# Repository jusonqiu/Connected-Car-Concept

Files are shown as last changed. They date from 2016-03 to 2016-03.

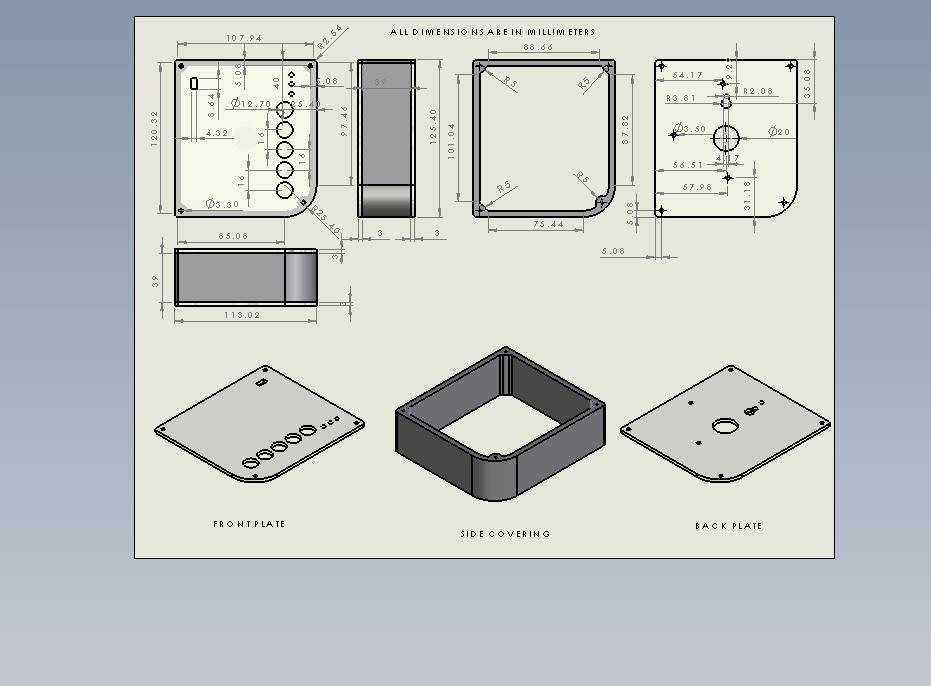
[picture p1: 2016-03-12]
Case Enclosure/Engineering Drawing.jpg

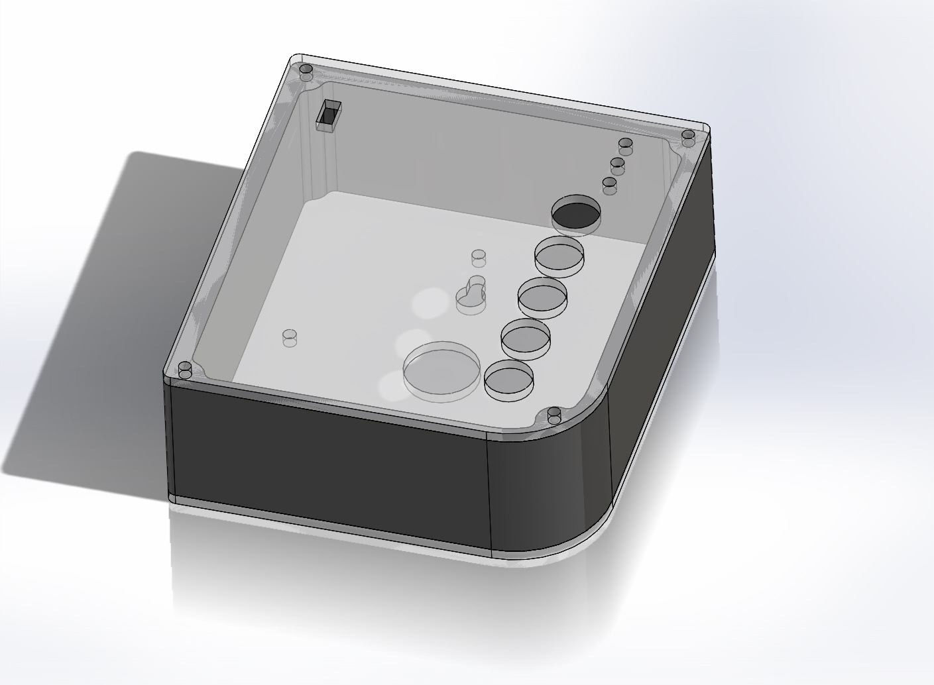
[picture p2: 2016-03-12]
Case Enclosure/GateBox Model.JPG

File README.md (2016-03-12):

# Connected Car Concept

The Connected Car Project, GateBox, allows you to operate your garage door and front lawn lights from the car's dashboard itself. It does this by having a smartphone interact with a gateway panel (the GateBox panel) that is placed within the garage. The smartphone is mirrored onto the car's dashboard. This is possible using a number of Connected Car features which are likely to grow popular in the future such as: Android Auto, Apple CarPlay, MirrorLink, AppLink, etc. This project was entered into the Microsoft Imagine Cup competition of 2015.

Please watch the introduction video below:

<div style="text-align: center">
<a href="http://www.youtube.com/watch?feature=player_embedded&v=YNrUQAdRSC8
" target="_blank">Connected Car Demonstration</a>
</div>

The Github.io page is can be seen [here](http://shafeeqr2.github.io/Connected-Car-Concept/ "GateBox").
## Opensource
Since the Microsoft Imagine Cup competition, this project has been released on Github in hopes that it can be improved upon. The orignal app developed is in the "Windows Application Folder". Some of the files that were submitted to Microsoft judges are in the "Imagine Cup Files" folder. These files have been slightly modified since submission. 

## Where to Start?
First read the Bluetooth manuals. They are from the Bluetooth Special Interest Group and aim to teach how to develop Bluetooth Low Energy applications for a number of different platforms  - Android, iOS and Windows Phone.

For the electronics, there are two different ways to approach this project: The Simplified and Detailed way - One method uses a pre-existing Bluetooth LE chip and other method involves making this chip from scratch based on schematics provided. There is a Parts List and the Instructions version for the detailed and the simplified way. It is recommended that you start with the simplified way even if you plan to use the detailed way.

Read through the parts list for the electronics and the case enclosure in the "Parts List" folder. Then, read through the hardware and software instructions in the "Instructions" folder.

##Contribute

If you feel you can improve on a certain aspect of this project or expand upon it, please considering sharing it to be a part of this project.

If you have any questions or concerns, please contact me at: shafeeqr21@gmail.com.

## What are Connected Cars?

### The following expert is from a 2014 CABA (Continental Automated Building Association) report:

*The connected car market, while still in its infancy, has rapidly evolved from a niche capability available in select models to a perceived must-have in the car industry. A connected car, by definition, is one that maintains a wide area connection (typically cellular-based) and often also a local area network (typically Wi-Fi). Via these connections the car is able to send and receive information relevant to the trip/route and the car’s performance/condition.*

*An increasing number of vehicles are coming to market with the capability to support communications of various sorts. In 2013 more than one billion sensors were sold to the auto industry, more than doubling the 2009 levels[1]. While tethered and integrated solutions have dominated car connectivity to date, embedded connectivity solutions began appearing in 2014 with the number of such vehicles increasing in 2015 and beyond.*

*The connected car market is on the cusp of significant growth. A variety of market factors, from government regulations, to industry partnerships, to consumer demand, are propelling the connected car market forward. Consumers got a glimpse of the future of connected cars in 2014 as select models began rolling off the production line with these capabilities, but 2015 promises so much more in terms of number of connected vehicles and the services being delivered to those vehicles.* 

##

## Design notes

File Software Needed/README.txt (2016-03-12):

The Arduino v 1.0.6 and nRFgo Studio are available for download at the following link: https://goo.gl/C3nlrD

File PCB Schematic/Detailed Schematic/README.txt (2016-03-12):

The design has been modified since these files have been made.

Would appreciate it if someone could replace the two solid state relays with 4 mechanical relays (as shown in PCB V7 board.PNG in Simplified Schematic folder) and re-route all the wires and push the .brd and .sch files.

Thanks.

Shafeeq.

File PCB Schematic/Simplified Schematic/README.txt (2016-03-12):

The design can be further simplified if you decide to use your own Arduino UNO in which case you need not include the following materials onto PCB (Refer to "PCB V7 board.PNG"):

* DCJACK
* Diode D1
* Capacitors C1, C2, C3, C4
* ATMEGA328P IC1
* Voltage Regulator 7805T IC2
* Quartz Crystal 16MHZ Q1

It would be nice if someone can take the time to make a PCB without these items and in its place leave a line of male headers which would connect to the Arduino UNO as per the following pinouts:

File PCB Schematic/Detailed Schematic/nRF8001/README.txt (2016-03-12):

The schematics of Adafruit's nRF8001 Bluetooth Low Energy Module circuitry can be found on 

Adafruit's Github Repository: https://github.com/adafruit/Adafruit-Bluefruit-LE-nRF8001-PCB

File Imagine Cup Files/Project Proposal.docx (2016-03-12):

GATEBOX

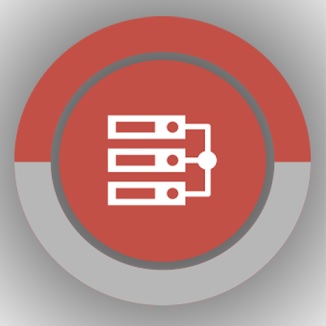
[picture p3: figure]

Shafeeq Rabbani

Paul Calinescu

Edgar Malchic

Esther Baruti

Why are we doing this?

We would like to make a positive impact in millions of households in the coming years by making the lives of homeowners more convenient and providing them with more control over their homes.

How are we going to do this?

Today, we have smartphones that can operate Bluetooth peripherals in a house and cars which can be paired with smartphones. Such cars are commonly referred to as connected cars. We would like to combine these two so that your connected car interacts with your house.

What are we making?

The GateBox.

There are two components to this system. First, is the panel which sits into the garage of your home. The second is the Windows Phone app which interacts with the panel in order to do some pretty interesting things in the garage.

Now, I know what you are thinking. How does the car enter the picture?

Currently, in the connected car market, solutions such as MirrorLink by Car Connectivity Consortium, AppLink by Ford, Android Auto by Google and CarPlay by Apple are gaining momentum. These solutions are meant to project the screen of the smartphone onto the dashboard of the car.

Before we go into details, we would like to demonstrate this system to you.

When the driver approaches the house, the app automatically detects the peripheral and connects to it. The driver, who is now in the driveway, is prompted to enter a passkey. Upon correct entry, the driver gains access to the control panel. From here, the driver can operate the garage door and the lights.

The Panel acts as a Bluetooth Low Energy peripheral and the smartphone acts as the central. We are using a custom GATT service.

The field of home automation along with connected cars is about to boom. According to the Continental Automated Buildings Association or CABA, the timing of this boom is put somewhere between late 2014 and mid 2015.

Hence, this is the best time for a system such as the GateBox. Our product touches on both matters, contributing and expanding this imminent boom.

The market for this system is geared towards people who live in homes with attached garages and drive cars.

Connected cars is a technology that will increase the intelligence of existing home automation systems. A more connected system will have a significant potential of becoming a smarter system. For a long time, your garage and your car have been two different systems. Now is the time to link these two systems so that you can control your garage door and garage lights directly from the car dash.

There has been talk in the market of connecting smartphones with cars with solutions such as MirrorLink from the Car Connectivity Consortium, and AppLink from Ford. We would like to take it one step further and connect your car with your garage.

Although there are a handful of similar projects we have encountered, none of them show signs of being consumer ready like the GateBox.

A system like this serves as a base that can easily be expanded upon in the future. In the future, we intend to further expand the capabilities of this product. It will have an IP address allowing it to connect to the network. That would allow us to collect data of this device to better serve the consumer. We would also like to give this product BACnet interoperability. BACnet is a communication protocol used in Building automation.

There are cars in the market today which have their own internet connection (I’m not sure about WIFI). Chevrolet is one of the manufacturers which are pushing for this. This option is available in models starting around the $15,000. Possible uses include having anonymous, critical and/or sensitive data uploaded to the cloud. This app which resides on your data-enabled smartphone and therefore our system would allow us to communicate with our car even when we are not home (i.e. work).

Our system is meant to be easily implemented in most garage with basic knowledge. The configuration of the system is meant to be intuitive and user friendly.

In addition to having full control of your garage and lights via your car, the GateBox panel located inside the garage will have physical switches mounted onto it allowing the homeowner manual control of their garage and lights.

GETTING PRODUCT INTO MARKET

Making an App for a car platform is a little bit more complex than making one for a smartphone. Not every smartphone platform is compatible with every mirroring software. Hence, in order to gain a broad consumer base, our app must be available in a number of smartphone platforms.

So how does Microsoft fit into this? Last year, Microsoft demonstrated the compatibility of Windows Phone with a MirrorLink-like solution. Considering their long partnership and contribution with the Car Connectivity Consortium the Windows Phone solution to MirrorLink may just be around the corner.

And while the Mirroring software industry is likely to grow exponentially in the coming years, we cannot ignore the already existing massive consumer base with Windows Automotive and QNX Car Infotainment systems present today which numbers in the tens of millions. We know exactly how to go about developing and testing our software application for inbuilt car infotainment systems and the costs involved. We are currently looking for auto manufacturers who are interested in implementing the GateBox software application.

We have a carried out a detailed research of every registration, certification and testing procedure we have to carry out in order to bring this product to the shelves. We are well aware of the procedures involved such as listing by Bluetooth Special Interest Group, electrical certification by the CSA group, Qualification by MirrorLink and AppLink, testing center fees and others related to registering a corporation. The details of these procedures and their cost are mentioned in our document. If we win the prize money, we have a very good idea of how we intend how to spend it in order to bring GateBox to the market.

The time is right for your car to join the smart movement. We see car manufacturers such as Chevrolet provide 4G LTE connectivity in cars starting from around $15,000. This will effectively put cars on the web and therefore make them accessible from anywhere. We see a future where we can control many of the things that we have never thought of controlling. Imagine being able to control things such as your sprinkler system if you don’t want it to turn on because it already rained that day. How about controlling your blinds because your house is letting you know that the sun is too bright and it would contribute to hotter temperatures inside the house. And what if you’ve forgotten your lights on in the house while you left in a hurry? Our system, the GateBox, will eventually be able to relay that information to your data enabled smartphone. What started as a system which can control your garage and lights could potentially turn into something which can solve many of our past, present and future problems and simplify our everyday tasks.

HOW WILL WE SPEND THE PRIZE MONEY IF WE WIN?

Task | Description | Cost
Registration as Corporation | Registration the corporation at Canadian Federal level with name search. | $250 CAD
Bluetooth Compliance Fees | Requirement to use Bluetooth product and will give us permission to use logo. For adopter members, the fee is $8000. However, as we would be a new company, we qualify for their Innovation Incentive Program (IIP) bringing the fees down to $2500. | $2500 USD
Bluetooth Testing and Bluetooth Qualification Review | This is carried out by a certified testing center of Bluetooth. We have been in contact with a testing center interested in testing our device. They have given us a quote of $6550. | $6650 USD
MirrorLink testing and certification | Testing is carried out by a certified body. Certification of our apps will allow the Android to work with ever growing MirrorLink installed car dashboards. | $ 5839.26 USD (or less if it is determined that app is not as complex).
Representative Business travel across US and Canada over a period of 2 years. | These are to establish business links with car manufacturers and other companies alike who are interested in partnering with us on mass production of the GateBox over a period | $10,000 USD
Purchase Pioneer Appradio 4 | This would be done to use for testing of our AppLink. | $600 USD
Testing for AppLink | Testing for Ford AppLink is carried out by a certified testing centre. AppLink is compatible with 3 smartphone platforms.i.e. Android, iOS and Blackberry. | $1400 x 3 = $4200 USD
Profile Tuning Suite Radio Module | This device is used for Bluetooth by ourselves before we send it out to the testing centre. It must be purchased from http://bluetoothstore.org/. | $99 USD
Safety certification of electrical product | We have sent the appropriate documentation for testing so that they can provide us with a quote. | $2500 USD
Software developer registration | Apple developer registration, Windows developer registration, Android developer registration and Blackberry developer registration for 3 consecutive years.
Purchasing software with commercial licenses
Purchasing smartphones for testing on different platforms | Alongside Windows Phone, we would like to test in Blackberry, Android and iOS. | $2000 USD
The remaining amount will be spent on costs we did not previously anticipate.

ELECTRONICS BEHIND THE GATEBOX

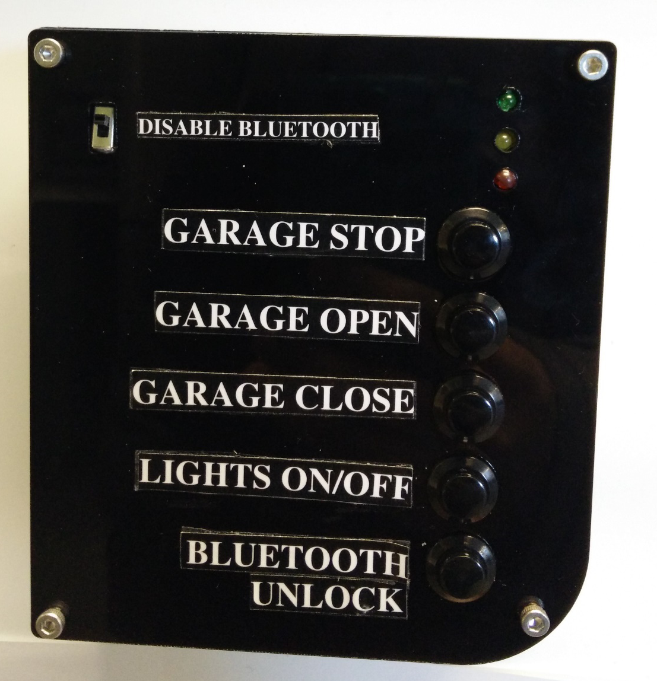
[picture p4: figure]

The GateBox panel is used to control the homeowner's garage door. Within the panel there is a custom relay shield that is controlled by a micro controller. On the main panel, there are 5 buttons. The 3 of the 5 buttons are used to stop, open, or close your garage. The fourth button is used to control the lights and the fifth button is used to unlock your Bluetooth panel. The sliding switch located at the top left is placed there for security purposes. If the homeowner decides to go on vacation and wants their panel to stop broadcasting, all they have to do is toggle the switch down. The LEDs are indicators to show an established connection between the panel and the car. The electronics inside the panel are:

1. main board
  a. This board consists of 4 mechanical relays, 5 push buttons, a barrel jack for power, a voltage regulator, resistors, diodes, capacitors, transistors etc. Please see parts list. The main board is powered by a 9V dc barrel jack adapter.
2. LED board which is attached to the main board by jumper cables.
3. Bluetooth low energy chip (nRF 8001 from Nordic) which is connected to the main board through header pins.

The device is meant to be up and running 24/7. Of the four mechanical relays, three are normally open and one is normally closed.

Button | State | Voltage
Garage Door Stop Button | Normally Closed | 0 - 24 VDC
Garage Door Open Button | Normally Open | 0 - 24 VDC
Garage Door Close Button | Normally Open | 0 - 24 VDC
Lights Button | Normally Open | 120 - 240 VAC

These relays can be operated by the push buttons or a command from the homeowner’s smartphone which is received by Bluetooth Low Energy chip. In either case, the command is first sent to the ATMega328PU microcontroller first which then sends a signal to the relay.

The enclosure of this device is made of 3mm thick acrylic. The device is meant to be wall mounted at least 5 feet above the ground.

The panel is compatible with most garage openers on the market today such as Liftmaster or Chamberlain. The contacts of the garage door and lights can be directly wired into the terminal blocks of the relay shield, and then the homeowner can begin accessing their garage door and lights via their car. We see a brilliant future where the world around us is further connected with smart sensors and devices which allow for a smoother and more effective interaction with the world around us.

Custom Board Bill of Materials

| | | | Total Costs | $28.7778
Part | Digikey/ Element14 Part No. | Manufacturer Part No. | Quantity | Picture | Cost
Atmega 328p Microcontroller | 68T2944 | ATMEGA328P-PU | 1 | | $3.24
16 MHz Crystal Oscillator | 18C1481 | XT9S20ANA16M | 1 | | $0.338
28 pin DIP IC Socket | 34P8056 | 4828-3004-CP | 1 | | $0.503
Rectifier Diode 1A, 50V | 10M8464 | 1N4001 | 1 | | $0.113
LM-7805-CT Voltage Reg. | MC7805CTG | MC7805CT-BPMS-ND | 1 | | $0.487
Switch Tactile SPST-NO | MJTP1230 | 679-2428-ND | 2 | | $0.1124
Terminal blocks | ED1623-ND | ED500/2DS | 4 | | $0.85
2.1mm DC Barrel Jack | CP-037A-ND | PJ-037A | 1 | | $1.23
100uF, 25V Electrolytic Cap. | 39T8695 | 25YXH100MEFC6.3X11 | 2 | | $0.075
22 pF, 50 V Ceramic Cap. | BC1034TR-ND | K220J15C0GF5TH5 | 2 | | $0.34
3mm LED, FWD V= 2.1V/I= 20 mA | 94T8843 | 703-0087 | 3 | | $0.184
10K Ω Resistor, 1W, 5% | 95W5667 | CFR100J10K | 8 | | $0.18
1K Ω Resistor, 1/4W, 5% | 25M8365 | CBT25J1K0 | 7 | | $0.32
6 Pin Male Header | 609-3263-ND | 68000-406HLF | 4 | | $0.24
G5V-1-DC Low Signal Relay | Z773-ND | G5V-1-DC5 | 4 | | $2.77
SPDT Sliding Switch | CKN9565-ND | OS102011MS2QN1 | 1 | | $0.54
DIODE GEN PURP | 1N4148TACT-ND | 1N4148TA | 4 | | $0.14
Transistor NPN | 2N3904FS-ND | 2N3904BU | 4 | | $0.26

NRF8001 BLE Board Bill of Materials

| | | | Total Costs | $23.7681
Part | Digikey/ Element 14/ Mouser Part No. | Manufacturer Part No. | Quantity | Picture | Cost
BLUETOOTH LW ENERGY nRF 8001 | 1490-1026-ND | nRF8001-R2Q32-T | 1 | | $5.72
HIGH-LOW LEVEL SHIFTER | 568-8150-1-ND | 74HC4050D,653 | 1 | | $0.606
Capacitors Solid SMD 10uF | 718-1126-2-ND | 293D106X96R3A2TE3 | 2 | | $0.229
LDO Voltage Regulators High | 576-2980-2-ND | MIC5225-3.3YM5 TR | 1 | | $1.28
CAPACITOR 15PF 50V, C0G, 5%, 0402 | 38K1652 | GRM1555C1H150JZ01D | 4 | | $0.106
CRYSTAL 32.7KHZ 12.5PF SMD | SE2415CT-ND | FC-255 32.7680K-A3 | 1 | | $1.69
Capacitor SMD 33 nF 25 VDC 0402 | 65-754-51 | GRM155R71E333KA88D | 1 | | $ 0.683
CAPACITOR, 0402 0.1NF 50V | 578095 | CM05CG101J50AH | 2 | | $1.00
Capacitor SMD 0.1uF 25volts | 478-7868-1-ND | 04023C104KAT2A | 1 | | $0.471
CAP, MLCC, X7R, 1NF, 50V, 0402 | 490-1303-1-ND | GRM155R71H102KA01D | 1 | | $0.368
CAP SMD 10UF 6.3V 20% 0402 | 81-GRM155R60J106ME4D | GRM155R60J106ME44D | 1 | | $0.444
CAP, 1.5pF 50V C0G ±0.1pF SMD | 490-8087-1-ND | GJM1555C1H1R5BB01D | 1 | | $0.10
CAP SMD 0402 22pF 50V C0G 5% | 581-04025A220J | 04025A220JAT2A | 1 | | $0.135
CAP SMD 0402 1.8pF 50V C0G | 81-GJM1555C1H1R8BB01 | GJM1555C1H1R8BB01D | 1 | | $0.283
CAP, MLCC, 2.2NF, 50V, X7R, 0402 | 2310511 | MC0402B222J500CT | 1 | | $0.11
RESISTOR, 10K, 0.06W, 0402, SMD | 541-10.0KLCT-ND | CRCW040210K0FKED | 1 | | $0.59
RES SMD 22K OHM 0.1% 1/10W 0603 | P22KDBCT-ND | ERA-3AEB223V | 1 | | $0.91
EMI Filter Beads, Chips & Arrays | 810-MMZ1608B121C | MMZ1608B121C | 1 | | $0.135
8.2nH SMD Inductor, 4.9GHz | 810-MHQ1005P8N2JT | MHQ1005P8N2JT | 1 | | $0.34
INDUCTOR, 10NH, 2%, 3.9GHZ, SMD | 994-0402CS-10NXGLU | 0402CS-10NXGLU | 1 | | $1.69
INDUCTOR, 15NH, 5%, 3.28GHZ, SMD | 994-0402CS-15NXJLU | 0402CS-15NXJLU | 1 | | $1.40
INDUCTOR,3.9NH, 5%, 9.5GHZ, SMD | 994-0402HP-3N9XJLU | 0402HP-3N9XJLU | 1 | | $1.54
INDUCTOR, 5.6NH, 2%, 6.5GHZ, SMD | 994-0402HP-5N6XGLU | 0402HP-5N6XGLU | 1 | | $1.34
CRYSTAL 16MHZ 9PF SMD | SER3636CT-ND | TSX-3225 16.0000MF18X-AC | 1 | | $0.91
U.FL SMD Antenna Connector | 798-U.FL-R-SMT10 | U.FL-R-SMT(10) | 1 | | $1.59

Schematic of Custom Board (created using Eagle CAD)

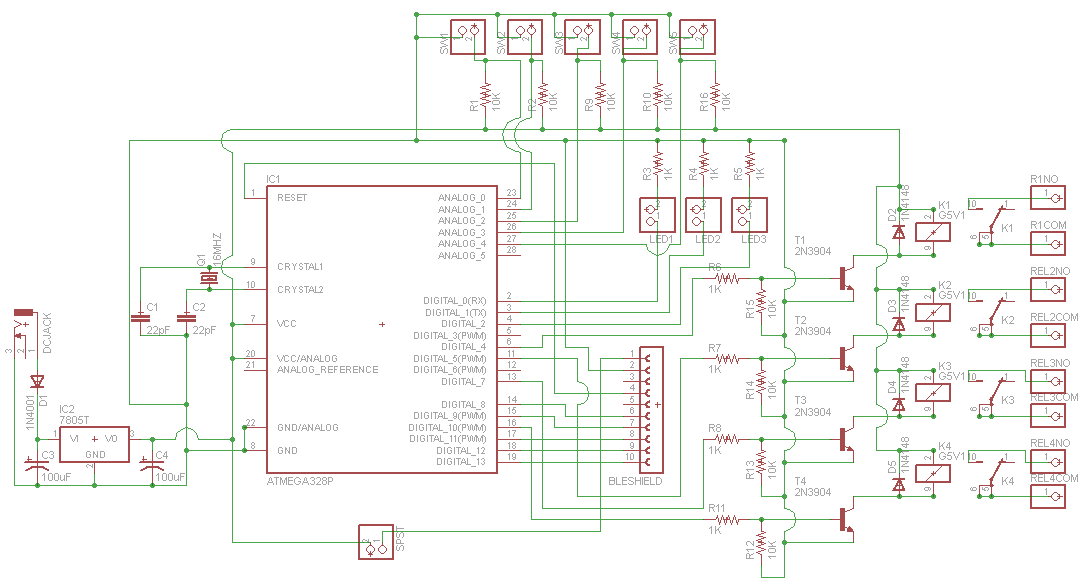
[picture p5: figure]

Layout of PCB (created using Eagle CAD)

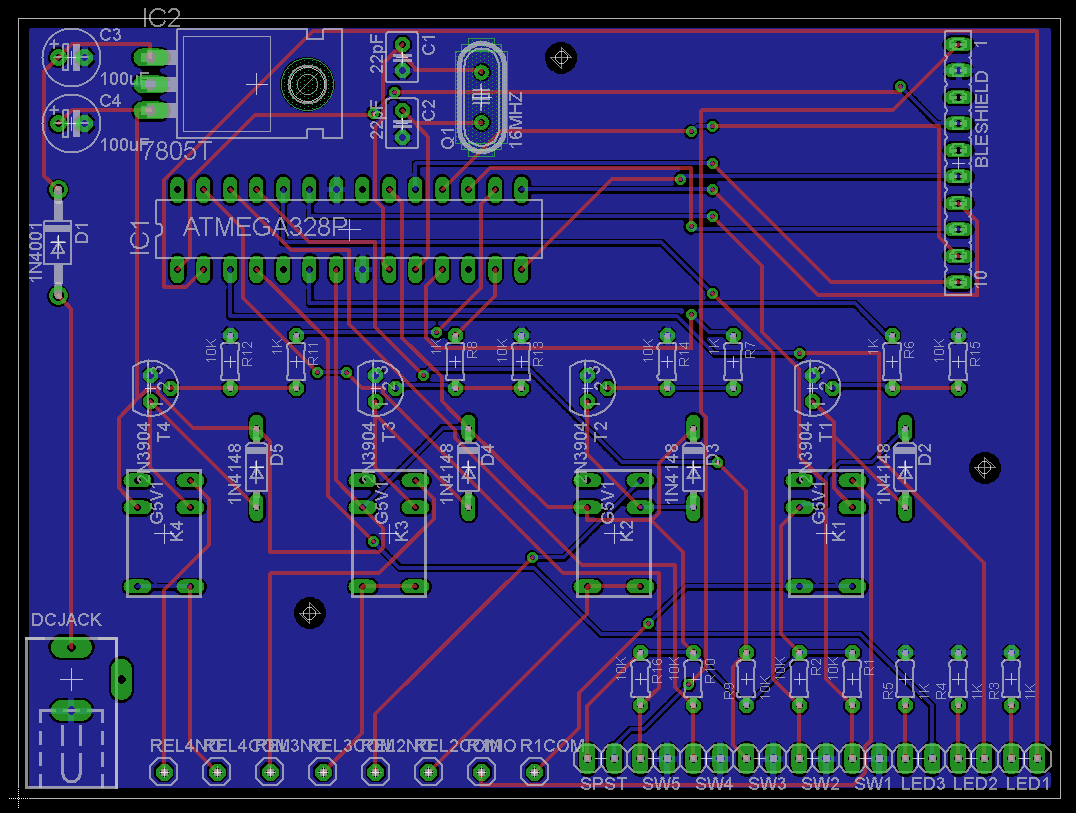
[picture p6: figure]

The GateBox panel was designed in Solidworks

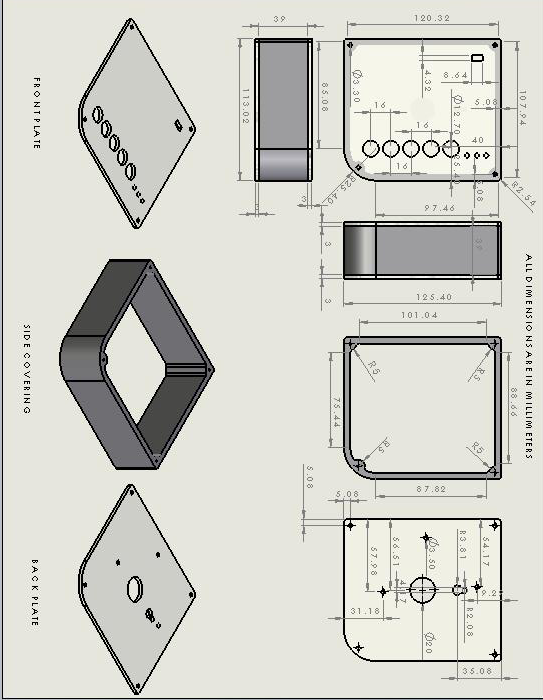
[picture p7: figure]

Safety Concerns

- The wall console/push button should be mounted at least five feet from the floor and the remote controls should be kept out of the hands of children. Children should never be allowed to play with or use the garage door opener remotes or wall pushbuttons. Homeowners should also keep a moving door in sight until it fully opens or closes.

Source: http://www.dasma.com/safetygdguide.asp

- Must be installed by a licensed electrician.
- Do not run any low voltage control wires close to the 120-volt power line. Do not run any wires through the same holes as the 120-volt power line in studs or cross ties. Either of these conditions will not comply with the NEC and may interfere with safe operation of the garage door operator.
- You will need 3 lengths of 2 conductor color coded minimum 22-gauge bell wire (phone wire) suitable for Class 2 installation. In Canada, this wire must be CSA certified.
- Emergency Stop button allows for the door to stop immediately whether it is going up or down.

Emergency Stop Button

Other Similar Projects/Products

HomeLink | http://homelink.com/home/welcome
Bosch Hackathon 2nd Place Winner (Not a competitor, has not produced a product out of this demo). | http://blog.bosch-si.com/categories/mobility/2014/10/how-can-we-bring-the-garage-into-the-car/
Other systems allow door activation over the Internet to allow home owners to open their garage door from their office for deliveries. | https://www.liftmaster.com/For-Homes/Garage-Door-Openers/Elite-Series/model-8550
The Overhead Door® Advanced Wall Console has been designed to not only provide homeowners with advanced security, but to deliver more control over their garage door opener, its lighting and opener performance status. The console is programmable to provide service reminders and contact information for the local Overhead Door Red Ribbon Distributor, making annual maintenance easy and convenient. | http://www.overheaddoor.com/garage-door-openers/Pages/advanced-wall-console.aspx http://www.overheaddoor.com/garage-door-openers/Pages/garage-door-opener-accessories.aspx
Bluetooth switch | http://www.ablenetinc.com/Assistive-Technology/Computer-Access/Blue2-Bluetooth-Switch
My door open iPhone app | https://itunes.apple.com/en/app/mydooropener-elite/id359774310?mt=8
iWUP | http://www.instructables.com/id/Garage-Door-Opener-with-iphone-Arduino-project/?ALLSTEPS

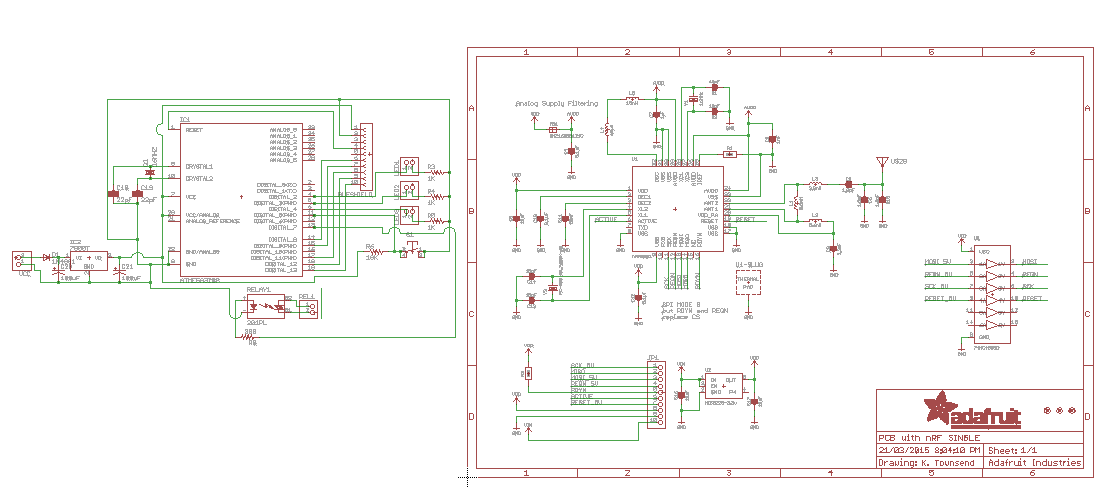
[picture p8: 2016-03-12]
PCB Schematic/Detailed Schematic/PCB with nRF/SINGLE RELAY/PCB with nRF Single Schematic.PNG

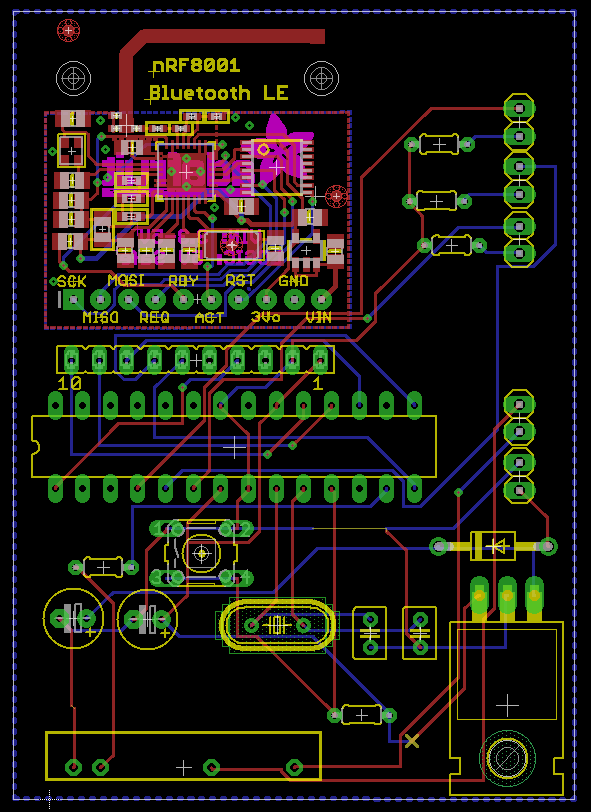
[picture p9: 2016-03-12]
PCB Schematic/Detailed Schematic/PCB with nRF/SINGLE RELAY/PCB with nRF Single Board.PNG

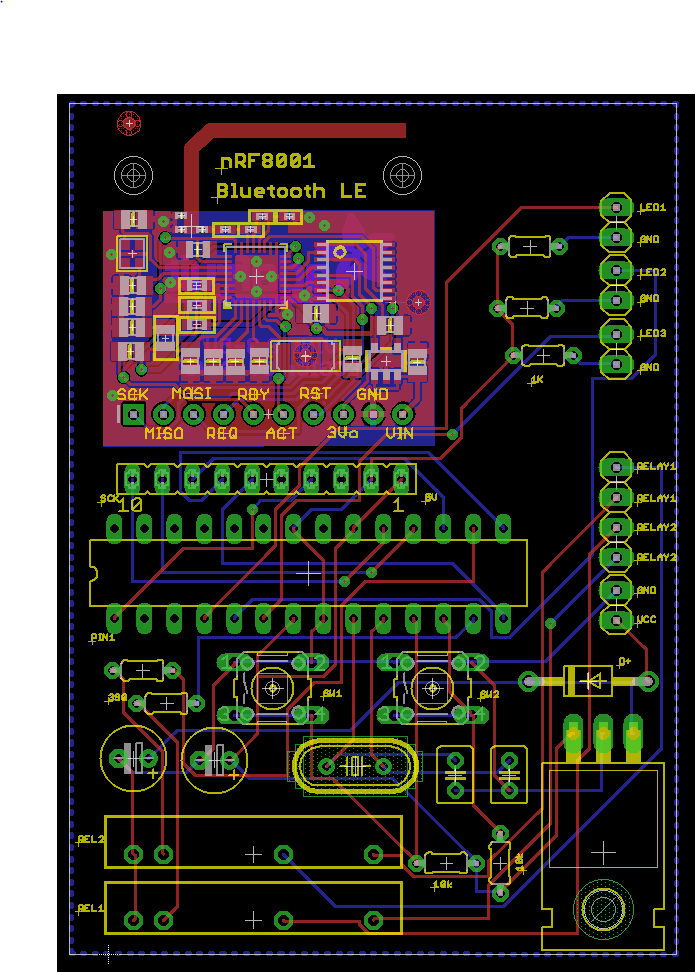
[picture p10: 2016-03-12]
PCB Schematic/Detailed Schematic/PCB with nRF/DUAL RELAY/PCB wih nRF board labeled.PNG

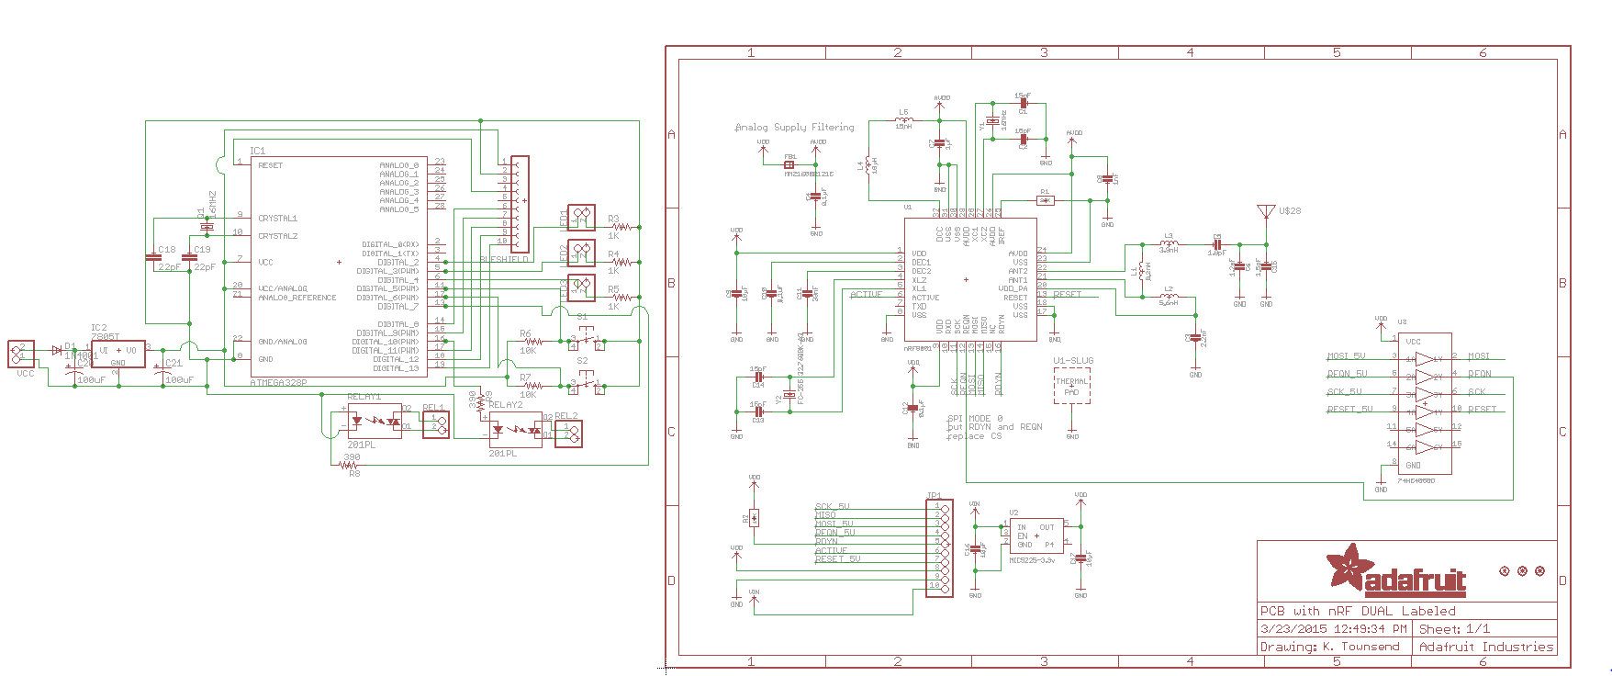
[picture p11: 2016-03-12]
PCB Schematic/Detailed Schematic/PCB with nRF/DUAL RELAY/PCB wih nRF schematic labeled.PNG

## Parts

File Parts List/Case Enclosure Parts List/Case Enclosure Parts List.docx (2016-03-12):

CASE ENCLOSURE PARTS LIST

You will need:

1. Access to a CNC machine
2. Access to 3D printer w/ ABS filament (preferably black colored filament)
3. M3-0.5 x 10mm DIN 912 Hex Drive Grade A2-70 Stainless Steel Socket Cap Screw (8 pieces)

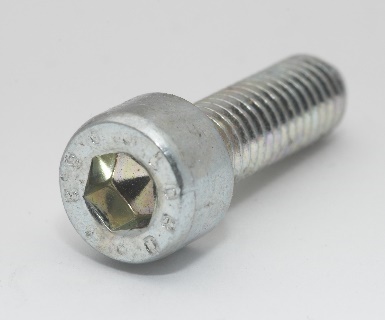
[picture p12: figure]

4. 3mm thick square acrylic plates (15 cm x 15 cm) (2 pieces) preferably black colored and glossy.
5. 3mm tap drill bit and a tapping drill

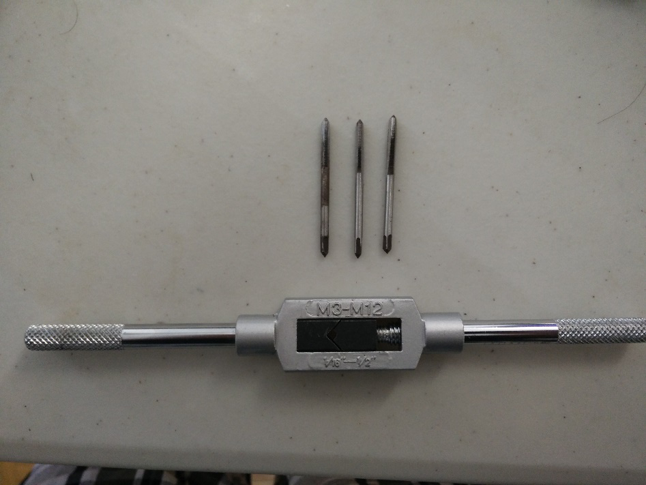
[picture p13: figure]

6. Allen key
7. Glue gun

CASE enclosure consists of the following parts:

A. The front plate
B. The back plate
C. The Covering

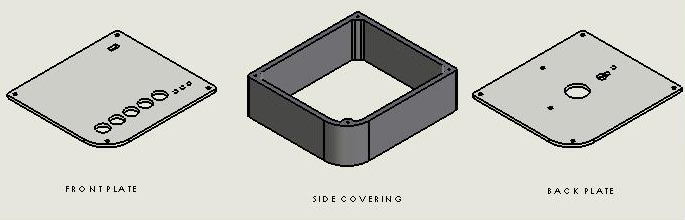
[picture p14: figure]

Instructions:

1. The front plate and back plate are 3mm thick acrylic plates (preferably black colored). Use the STEP files in the Case Enclosure Folder. The front_plate.STEP file back_plate.STEP file have to used to cut the acrylic plates into shape using a CNC.
2. The side_covering.STL file must be 3D printed with ABS filament.
3. Using the 3mm tapping drill bits and the hand tapping tool, carefully thread the 8 holes (4 on each side) of the side_covering.
4. Place the front panel on the side covering as shown below:

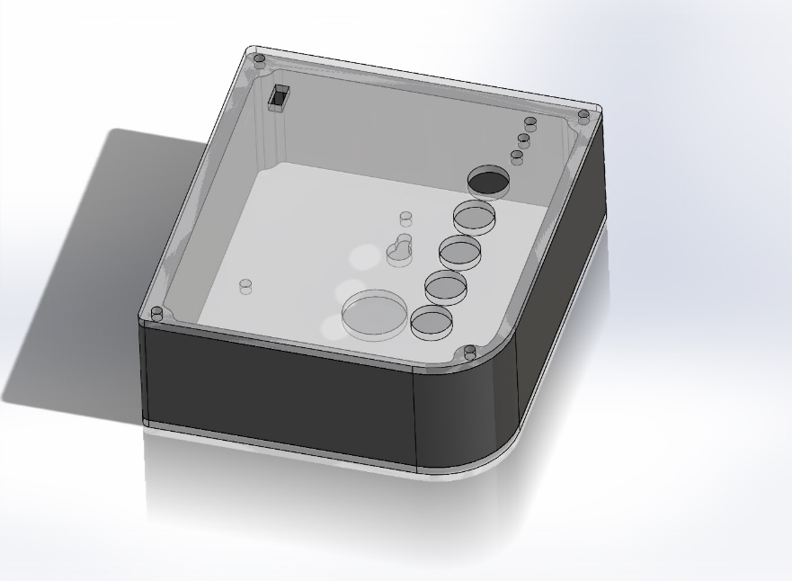
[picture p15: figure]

5. Place 4 screws and fix front plate onto the side covering. Make sure not to make it too tight – this can destroy the threads in the ABS plastic.
6. Fix the pushbuttons, the LEDs and switch onto the front plate as shown below. Use a glue gun where necessary. You may want to stick stickers to label the items.

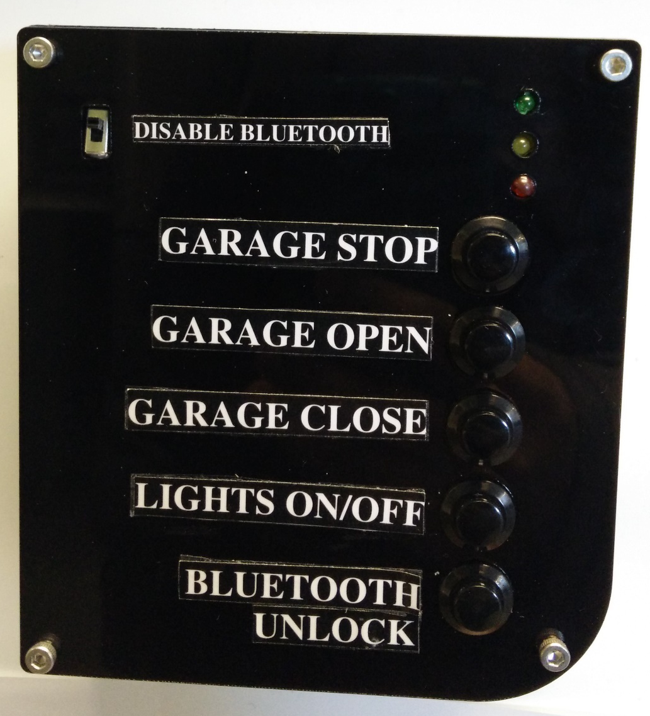
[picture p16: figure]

7. Solder connecting wires between the buttons, LEDs and switch onto the PCB with relays.
8. The large hole in the middle of the back plate is for wires to stick out from. These wires can connect the relays to compatible garage openers.
9. Fasten the back plate with the four remaining socket cap screws onto the side covering. Make sure you don’t tighten them too much as it can destroy the threads in the ABS plastic side covering.
10. The Gate box device can now be mounted onto a nail on a wail like a clock.

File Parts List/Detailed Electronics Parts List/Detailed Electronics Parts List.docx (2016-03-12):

## GATEBOX: DETAILED ELECTRONICS PARTS LIST

By Shafeeq Rabbani


## Introduction

As this approach involves creating everything from scratch and printing it all on a single PCB. Currently, there isn’t a complete version of the circuit. There is one that is almost complete: Would appreciate it if someone could replace the two solid state relays in the “PCB with nRF/Dual Relay” folder, with 4 mechanical relays (as shown in PCB V7 board.PNG and PCB V7 Schematic.PNG in Simplified Schematic folder) and re-route all the wires and push the .brd and .sch files. The Detailed Schematic/nRF8001 folder also contains .sch and .brd files of the nRF8001 chip from Nordic Semiconductors and Adafruit, the manufacturers of the nRF8001 chip and the Bluetooth Low Energy module respectively.

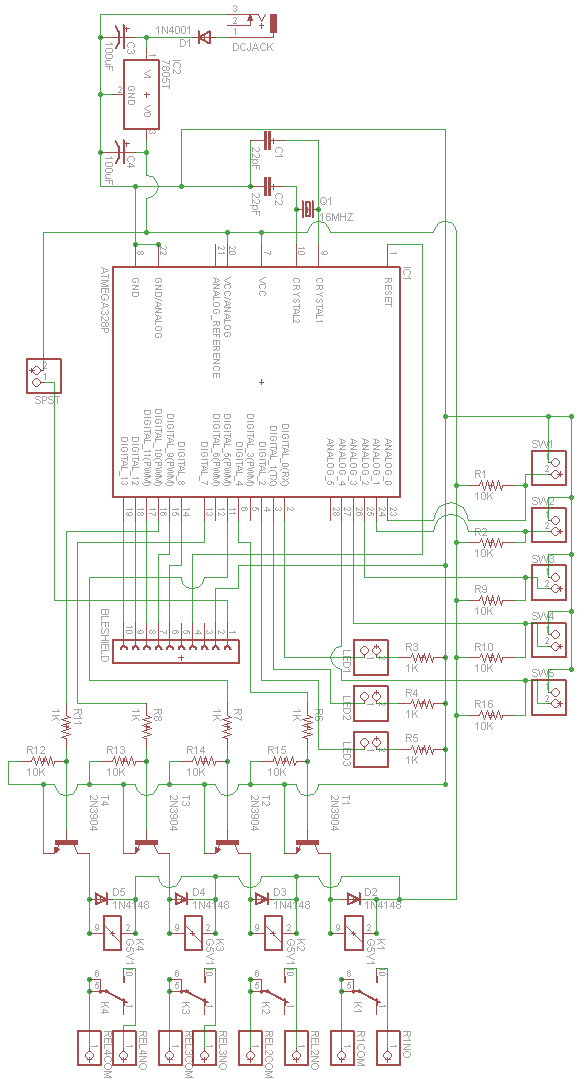
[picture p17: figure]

## Custom Arduino Board + GateBox Accessories

As the GateBox device is expected to be up and running for 24/7, you will require a 5V DC power supply that can power the Arduino UNO.

Part | Digikey/ Element14 Part No. | | Manufacturer Part No. | Quantity | Picture | Cost

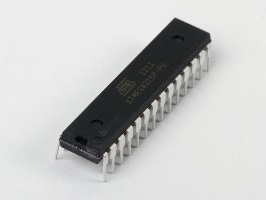
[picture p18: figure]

Atmega 328p Microcontroller | 68T2944 | | ATMEGA328P-PU | 1 | | $3.24

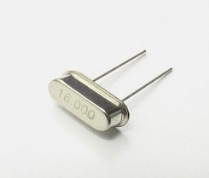
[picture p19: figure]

16 MHz Crystal Oscillator | 18C1481 | | XT9S20ANA16M | 1 | | $0.338


28 pin DIP IC Socket | 34P8056 | | 4828-3004-CP | 1 | | $0.503


Rectifier Diode 1A, 50V | 10M8464 | | 1N4001 | 1 | | $0.113


LM-7805-CT Linear Voltage Regulator | MC7805CTG | | MC7805CT-BPMS-ND | 1 | | $0.487

ED500/2DS On Shore Technology Inc | ED1623-ND DigiKey Electronics

Terminal blocks | ED1623-ND | | ED500/2DS | 4 | | 0.85

DC Barrel Power Jack/Connector

2.1mm DC Barrel Jack | CP-037A-ND | | PJ-037A | 1 | | $1.23


100uF, 25V Aluminum Electrolytic Capacitor | 39T8695 | | 25YXH100MEFC6.3X11 | 2 | | $0.075


22 pF, 50 V Ceramic Capacitors | BC1034TR-ND | | K220J15C0GF5TH5 | 2 | | $0.34


3mm LED, FWD V= 2.1V FWD I= 20mA | 94T8843 | | 703-0087 | 3 | | $0.184


10K Ω Resistor, 1W, 5% | 95W5667 | | CFR100J10K | 8 | | $0.18


1K Ω Resistor, 1/4W, 5% | 25M8365 | | CBT25J1K0 | 7 | | $0.32

68000-406HLF FCI | 609-3263-ND DigiKey Electronics

6 Pin Male Header | 609-3263-ND | | 68000-406HLF | 4 | | $0.24
G5V-1-DC Low Signal Relay | | Z773-ND | G5V-1-DC5 | 4 | | 2.77

OS102011MS2QN1 C&K Components | CKN9565-ND DigiKey Electronics

SPDT Sliding Switch | | CKN9565-ND | OS102011MS2QN1 | 1 | | 0.54
DIODE GEN PURP | | 1N4148TACT-ND | 1N4148TA | 4 | | 0.14

2N3904BU Fairchild Semiconductor | 2N3904FS-ND DigiKey Electronics

Transistor NPN | | 2N3904FS-ND | 2N3904BU | 4 | | 0.26
SWITCH PUSH SPST-NO | | EG1900-ND | RP3502ABLK | 5 | | | 2.80

## nRF8001 BLE Board

Part | Digikey/ Elfa Distrelec/ Element 14/ Mouser Part No. | Manufacturer Part No. | Quantity | Picture | Cost


BLUETOOTH LW ENERGY nRF 8001 | 1490-1026-ND | nRF8001-R2Q32-T | 1 | | $5.72
Buffers & Line Drivers HEX HIGH-LOW LEVEL SHIFTER | 568-8150-1-ND | 74HC4050D,653 | 1 | | $0.606
Tantalum Capacitors Solid SMD 10uF | 718-1126-2-ND | 293D106X96R3A2TE3 | 2 | | $0.229

Micrel MIC5225-3.3YM5 TR

LDO Voltage Regulators High | 576-2980-2-ND | MIC5225-3.3YM5 TR | 1 | | $1.28
CERAMIC CAPACITOR 15PF 50V, C0G, 5%, 0402 | 38K1652 | GRM1555C1H150JZ01D | 4 | | $0.106

FC-255 32.7680K-A3 EPSON | SE2415CT-ND DigiKey Electronics

CRYSTAL 32.768KHZ 12.5PF SMD | SE2415CT-ND | FC-255 32.7680K-A3 | 1 | | $1.69
Capacitor SMD 33 nF 25 VDC 0402 | 65-754-51 | GRM155R71E333KA88D | 1 | | $ 0.683
CAPACITOR, 0402 0.1NF 50V | 578095 | CM05CG101J50AH | 2 | | $1.00
Capacitor SMD/SMT 0.1uF 25volts | 478-7868-1-ND | 04023C104KAT2A | 1 | | $0.471
CAP, MLCC, X7R, 1NF, 50V, 0402 | 490-1303-1-ND | GRM155R71H102KA01D | 1 | | $0.368

Murata Electronics GRM155R60J106ME44D

Ceramic Capacitors MLCC - SMD 10UF 6.3V 20% 0402 | 81-GRM155R60J106ME4D | GRM155R60J106ME44D | 1 | | $0.444
Capacitor, 1.5pF 50 V DC C0G Dielectric ±0.1pF SMD | 490-8087-1-ND | GJM1555C1H1R5BB01D | 1 | | $0.10

AVX 04025A220JAT2A

Capacitors MLCC - SMD 0402 22pF 50V C0G 5% | 581-04025A220J | 04025A220JAT2A | 1 | | $0.135
Capacitors MLCC - SMD 0402 1.8pF 50V C0G +/-0.1pF | 81-GJM1555C1H1R8BB01 | GJM1555C1H1R8BB01D | 1 | | $0.283
CAPACITOR, MLCC, 2.2NF, 50V, X7R, 0402 | 2310511 | MC0402B222J500CT | 1 | | $0.11


RESISTOR, 10K, 0.063W, 1%, 0402, SMD | 541-10.0KLCT-ND | CRCW040210K0FKED | 1 | | $0.59
RES SMD 22K OHM 0.1% 1/10W 0603 | P22KDBCT-ND | ERA-3AEB223V | 1 | | $0.91
EMI Filter Beads, Chips & Arrays Ferrite Chip Beads | 810-MMZ1608B121C | MMZ1608B121C | 1 | | $0.135
8.2nH SMD Inductor, SRF: 4.9GHz Q: 23 550mA dc 160mΩ Rdc | 810-MHQ1005P8N2JT | MHQ1005P8N2JT | 1 | | $0.34
INDUCTOR, RF, 10NH, 2%, 3.9GHZ, SMD | 994-0402CS-10NXGLU | 0402CS-10NXGLU | 1 | | $1.69
INDUCTOR, RF, 15NH, 5%, 3.28GHZ, SMD | 994-0402CS-15NXJLU | 0402CS-15NXJLU | 1 | | $1.40
INDUCTOR, RF, 3.9NH, 5%, 9.5GHZ, SMD | 994-0402HP-3N9XJLU | 0402HP-3N9XJLU | 1 | | $1.54
INDUCTOR, RF, 5.6NH, 2%, 6.5GHZ, SMD | 994-0402HP-5N6XGLU | 0402HP-5N6XGLU | 1 | | $1.34


CRYSTAL 16MHZ 9PF SMD | SER3636CT-ND | TSX-3225 16.0000MF18X-AC3 | 1 | | $0.91
U.FL SMD Antenna Connector | 798-U.FL-R-SMT10 | U.FL-R-SMT(10) | 1 | | $1.59

You will need access to a machine that can print PCBs and solder SMD components onto them. This will likely be an electronics manufacturer.

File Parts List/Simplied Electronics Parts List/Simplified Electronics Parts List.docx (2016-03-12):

## GATEBOX: PARTS LIST (SIMPLIFIED)

By Shafeeq Rabbani


## Introduction

This parts list is where we recommend you start testing this project. It is considered simplified because rather than making the complex circuitry of the Bluetooth Low Energy chip, we use a pre-existing chip. You can approach this in the following ways:

A. You can use an Arduino UNO board, a Bluetooth Low Energy Chip and a perf board for the relay circuitry. This is the simplest possible approach to this project.
B. You can use an Arduino UNO board, a Bluetooth Low Energy Chip and a PCB (from PCB V7.brd). This is a lot like the previous method but can speed up development since you will not have to solder as many parts. As you are already using an Arduino UNO, you will not have to solder all the parts on the resulting PCB.
C. You can solder all the components on the PCB V7.brd board (the PCB has place for Arduino UNO’s components) and use a Bluetooth Low Energy chip.

## What you will need:

1. As the GateBox device is expected to be up and running for 24/7, you will require a 5V DC power supply that can power the Arduino UNO.
2. A Bluetooth Low Energy module from Nordic Semiconductors called “nRF8001”. There are two options you can choose from that already have the circuitry built in.


Option 1 | Option 2
The Adafruit Bluetooth Low Energy nRF8001 breakout board (https://www.adafruit.com/product/1697) | The RedBearLab BLE shield (http://redbearlab.com/bleshield/)

## Parts List for Option A and B

Part | Digikey/ Element14 Part No. | | Manufacturer Part No. | Quantity | Picture | Cost (CANADIAN $)

A000066 Arduino | 1050-1024-ND DigiKey Electronics

ARDUINO UNO REV 3 | 1050-1024-ND | | A000066 | 1 | | 33.43

ED500/2DS On Shore Technology Inc | ED1623-ND DigiKey Electronics

Terminal blocks | ED1623-ND | | ED500/2DS | 4 | | 0.85


3mm LED, FWD V= 2.1V FWD I= 20mA | 94T8843 | | 703-0087 | 3 | | $0.184


10K Ω Resistor, 1W, 5% | 95W5667 | | CFR100J10K | 8 | | $0.18


1K Ω Resistor, 1/4W, 5% | 25M8365 | | CBT25J1K0 | 7 | | $0.32

68000-406HLF FCI | 609-3263-ND DigiKey Electronics

6 Pin Male Header | 609-3263-ND | | 68000-406HLF | 4 | | $0.24

G5V-1-DC5 Omron Electronics Inc-EMC Div | Z773-ND DigiKey Electronics

G5V-1-DC Low Signal Relay | | Z773-ND | G5V-1-DC5 | 4 | | 2.77

OS102011MS2QN1 C&K Components | CKN9565-ND DigiKey Electronics

SPDT Sliding Switch | | CKN9565-ND | OS102011MS2QN1 | 1 | | 0.54

1N4148TA Fairchild Semiconductor | 1N4148TACT-ND DigiKey Electronics

DIODE GEN PURP | | 1N4148TACT-ND | 1N4148TA | 4 | | 0.14

2N3904BU Fairchild Semiconductor | 2N3904FS-ND DigiKey Electronics

Transistor NPN | | 2N3904FS-ND | 2N3904BU | 4 | | 0.26

RP3502ABLK E-Switch | EG1900-ND DigiKey Electronics

SWITCH PUSH SPST-NO | | EG1900-ND | RP3502ABLK | 5 | | 2.80


Prototype Board (Not needed for Option B) | | Any brand of your choosing | Any brand of your choosing | 1 | | -


24-30 AWG wire (For connections on perf board. Alternatively, you can strip open a CAT5 cable and use the one of the 8 small wires instead.) | | Any brand of your choosing | Any brand of your choosing | - | | -
Soldering iron and Solder | | Any brand of your choosing | Any brand of your choosing | - | - | -

## Parts List for Option C

Part | Digikey/ Element14 Part No. | | Manufacturer Part No. | Quantity | Picture | Cost (CANADIAN $)


Atmega 328p Microcontroller | 68T2944 | | ATMEGA328P-PU | 1 | | $3.24


16 MHz Crystal Oscillator | 18C1481 | | XT9S20ANA16M | 1 | | $0.338


28 pin DIP IC Socket | 34P8056 | | 4828-3004-CP | 1 | | $0.503


Rectifier Diode 1A, 50V | 10M8464 | | 1N4001 | 1 | | $0.113


LM-7805-CT Linear Voltage Regulator | MC7805CTG | | MC7805CT-BPMS-ND | 1 | | $0.487
Terminal blocks | ED1623-ND | | ED500/2DS | 4 | | 0.85

DC Barrel Power Jack/Connector

2.1mm DC Barrel Jack | CP-037A-ND | | PJ-037A | 1 | | $1.23


100uF, 25V Aluminum Electrolytic Capacitor | 39T8695 | | 25YXH100MEFC6.3X11 | 2 | | $0.075


22 pF, 50 V Ceramic Capacitors | BC1034TR-ND | | K220J15C0GF5TH5 | 2 | | $0.34
3mm LED, FWD V= 2.1V FWD I= 20mA | 94T8843 | | 703-0087 | 3 | | $0.184
10K Ω Resistor, 1W, 5% | 95W5667 | | CFR100J10K | 8 | | $0.18
1K Ω Resistor, 1/4W, 5% | 25M8365 | | CBT25J1K0 | 7 | | $0.32
6 Pin Male Header | 609-3263-ND | | 68000-406HLF | 4 | | $0.24
G5V-1-DC Low Signal Relay | | Z773-ND | G5V-1-DC5 | 4 | | 2.77
SPDT Sliding Switch | | CKN9565-ND | OS102011MS2QN1 | 1 | | 0.54
DIODE GEN PURP | | 1N4148TACT-ND | 1N4148TA | 4 | | 0.14
Transistor NPN | | 2N3904FS-ND | 2N3904BU | 4 | | 0.26
SWITCH PUSH SPST-NO | | EG1900-ND | RP3502ABLK | 5 | | 2.80

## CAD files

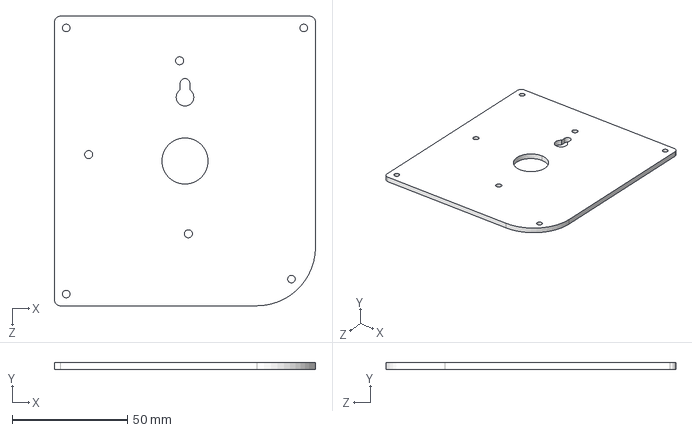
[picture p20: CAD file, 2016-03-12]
Case Enclosure/SolidWorks Files/back_plate.STEP
113.0 x 3.00 x 125.4 mm

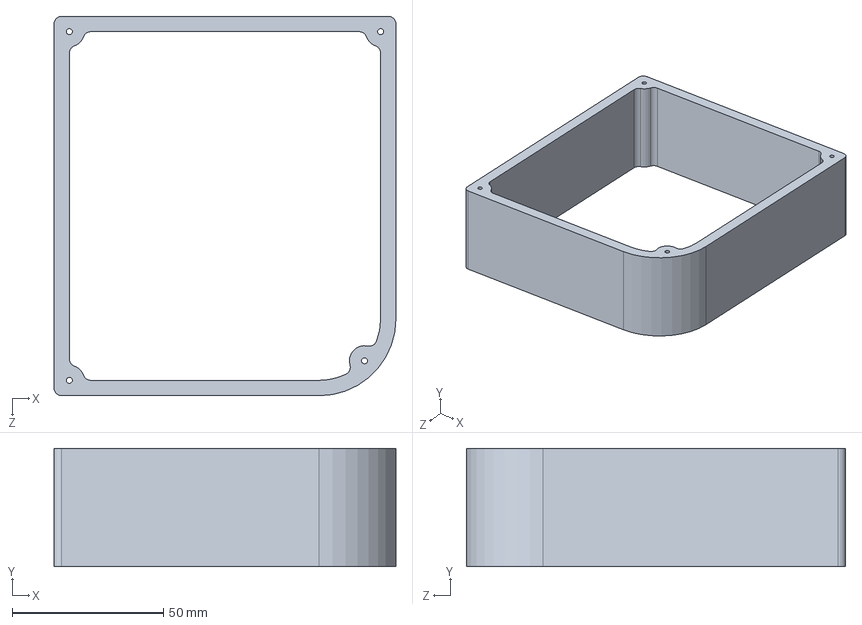
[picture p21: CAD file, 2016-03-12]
Case Enclosure/SolidWorks Files/side_covering.SLDPRT
113.0 x 39.0 x 125.4 mm

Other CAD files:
Case Enclosure/SolidWorks Files/front_plate.STEP
Case Enclosure/SolidWorks Files/back_plate.SLDPRT
Case Enclosure/SolidWorks Files/front_plate.SLDPRT

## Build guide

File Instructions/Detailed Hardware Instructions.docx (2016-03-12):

GATEBOX: DETAILED HARDWARE INSTRUCTIONS

By Shafeeq Rabbani


## Introduction

As the PCB machine printer does most of the job when it comes to hardware instructions, this section is quite straight forward. Currently, there isn’t a complete version of the circuit. There is one that is almost complete: Would appreciate it if someone could replace the two solid state relays in the “PCB with nRF/Dual Relay” folder, with 4 mechanical relays (as shown in PCB V7 board.PNG and PCB V7 Schematic.PNG in Simplified Schematic folder) and re-route all the wires and push the .brd and .sch files. The Detailed Schematic/nRF8001 folder also contains .sch and .brd files of the nRF8001 chip from Nordic Semiconductors and Adafruit, the manufacturers of the nRF8001 chip and the Bluetooth Low Energy module respectively.

## Pinout for Relays, Push Buttons, LEDs and Slide Switch

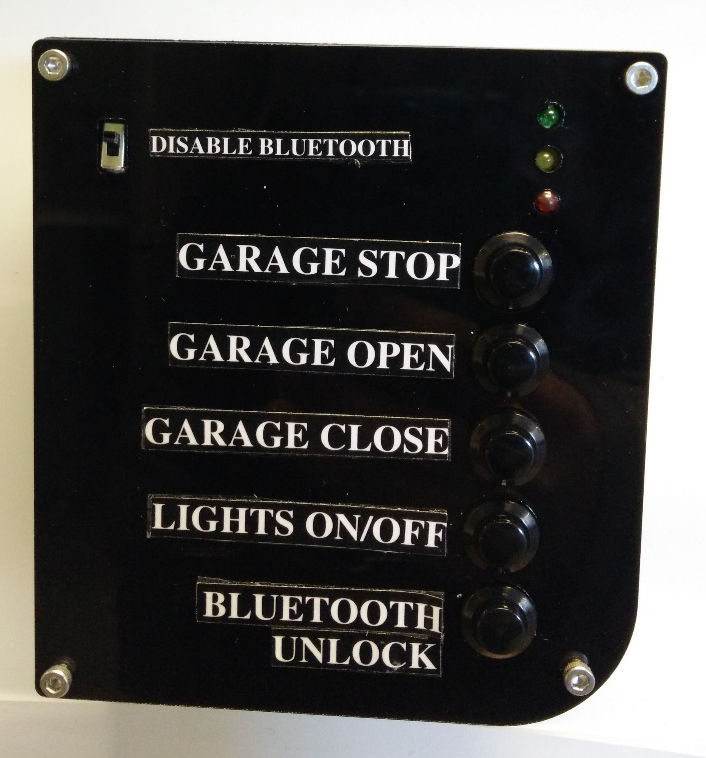
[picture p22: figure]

Just for reference, here are the pinouts.

The Relays and LEDs are operated by output pins and the Push Buttons are operated by input pins.

The following table shows which pin corresponds to what function in the Arduino code “ConnectedCar” and “ConnectedCarTest”. Solder these connections or use header pins from the Arduino to the relay circuit board.

Output pins

Component | Function | Pin Number
Relays | Garage Stop | 7
| Garage Open | 4
| Garage Close | 5
| Lights On/Off | 10
LEDs | LED: Red | 3
| LED: Green | A5
| LED: Yellow | 2

Input pins

Component | Function | Pin Number
Push Button | Garage Stop | A0
| Garage Open | A1
| Garage Close | A2
| Lights On/Off | A3
| Bluetooth Unlock | A4
Slide Switch | Disable Bluetooth | This switch must be on the 5V wire connection between the Arduino and the Bluetooth Low Energy Chip. Hence, “Disable Bluetooth” turns of the power itself to the Bluetooth Chip.

If you are having trouble identifying which pin on the Atmega328p corresponds which pin number, use this diagram below:

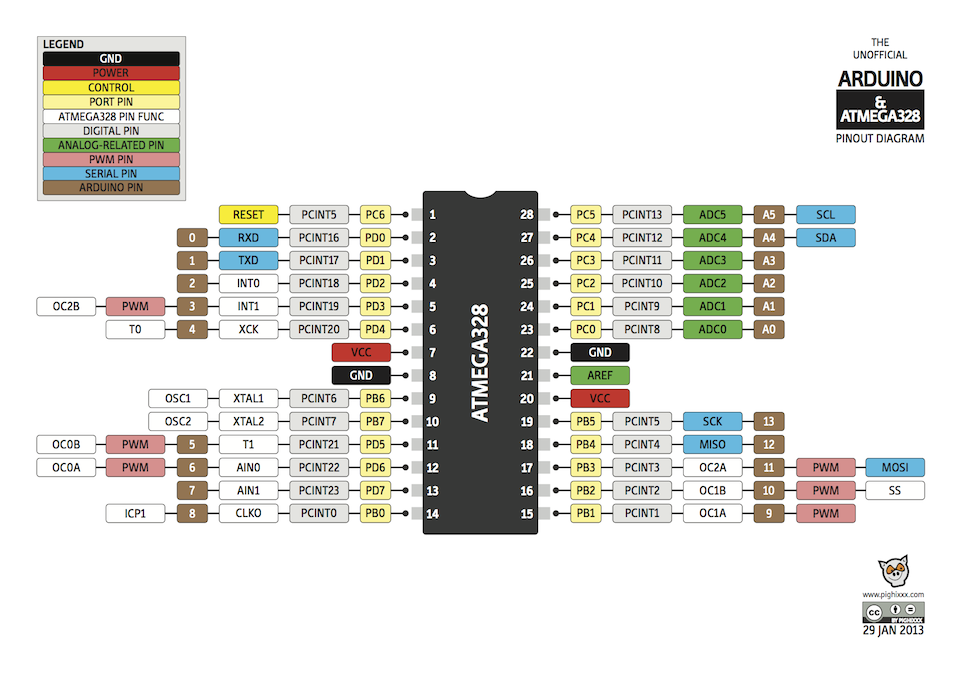
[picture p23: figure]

## Final Steps:

Connect wires from pre-existing garage door openers into the terminal blocks. Refer to the Garage Door Openers on Market (Manuals) folder to get an idea of how majority of the garage door openers on the market work. Do the same for lights. As this involves working with the mains, this task must be carried out with the aid of a professional certified electrician.

Connect the 5V dc jack onto the Arduino to power it. You can now insert the electronics into the GateBox panel and close the seal to power it up.

Your GateBox panel is now ready.

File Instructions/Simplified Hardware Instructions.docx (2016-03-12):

GATEBOX: SIMPLIFIED HARDWARE INSTRUCTIONS

By Shafeeq Rabbani


## Introduction

As mentioned in the Simplified Electronics Parts List document, You can approach this in the following ways:

A. You can use an Arduino UNO board, a Bluetooth Low Energy Chip and a perf board for the relay circuitry. This is the simplest possible approach to this project.
B. You can use an Arduino UNO board, a Bluetooth Low Energy Chip and a PCB (from PCB V7.brd). This is a lot like the previous method but can speed up development since you will not have to solder as many parts. As you are already using an Arduino UNO, you will not have to solder all the parts on the resulting PCB.
C. You can solder all the components on the PCB V7.brd board (the PCB has place for Arduino UNO’s components) and use a Bluetooth Low Energy chip.

## Choosing a Bluetooth Low Energy Chip

There are two options you can chose from:

Option 1 | Option 2
The Adafruit Bluetooth Low Energy nRF8001 breakout board (https://www.adafruit.com/product/1697) | The RedBearLab BLE shield (http://redbearlab.com/bleshield/)

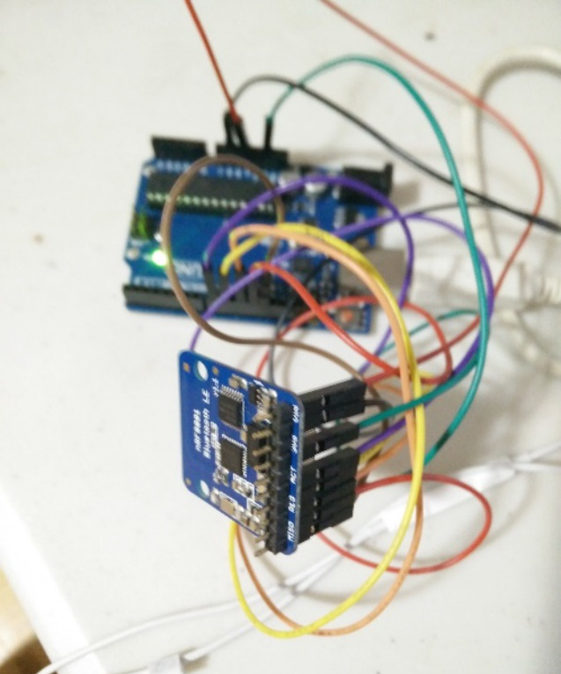
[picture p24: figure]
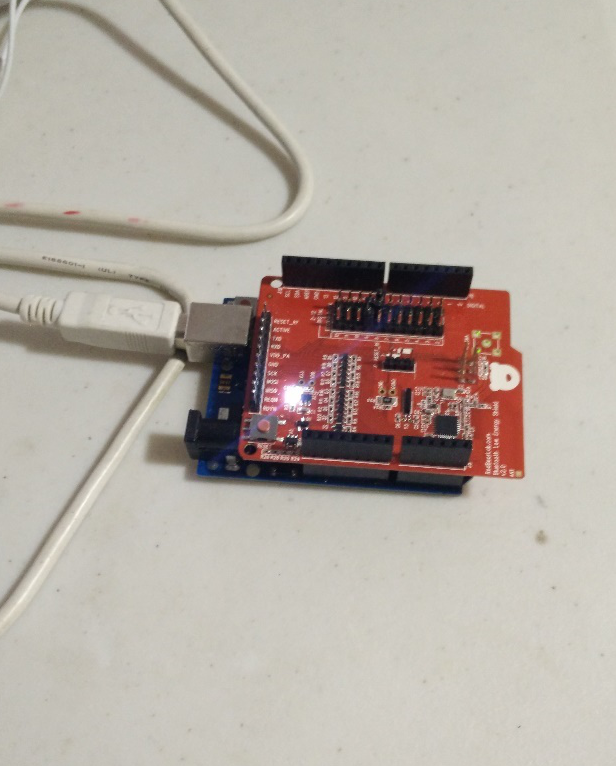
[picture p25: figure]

If you go with this option, you will need 8 male-female header cables, a row of 10 male headerpins , a soldering iron and some solder. Solder the header pins onto the nRF8001 breakout board. | The pins of the RedBearLab shield attach onto the Arduino UNO so you won’t need any header wires. However from experience, the Case Enclosure is not big enough to fit the Arduino UNO with a shield along with the relays board and other electronics. You may need a thicker case Elosure (by modifying the thickness in the side_covering.SLDPRT flie) or make a new one entirely from scratch).

## Wire the Arduino UNO to the Bluetooth Low Energy Chip

You should follow the same pinout to interface the Arduino UNO board to the Bluetooth Low Energy chip from the previous step regardless of which option you chose. If you are using the RedBearLab shield, this pinout should not be a problem as there is only one way to fix the shield onto the Arduino UNO board. If you are using the Bluetooth Low Energy module breakout board from Adafruit, make sure to follow this pinout:

Arduino UNO pin | Bluetooth Low Energy Chip pin
13 | SCK (connects to SPI clock)
12 | MISO (connects to SPI MISO)
11 | MOSI (connects to SPI MOSI)
9 | REQ (connects to SPI chip select pin)
8 | RDY is the interrupt pin from the nRF8001
None | ACT
RESET | RST
None | 3V OUT
GND | GND (connects to Ground pin on Arduino UNO)
5V | VIN (connects to 5V pin on Arduino UNO)

Note: It may be easier and lesser prone to error if you connect the header cables using the color code shown.

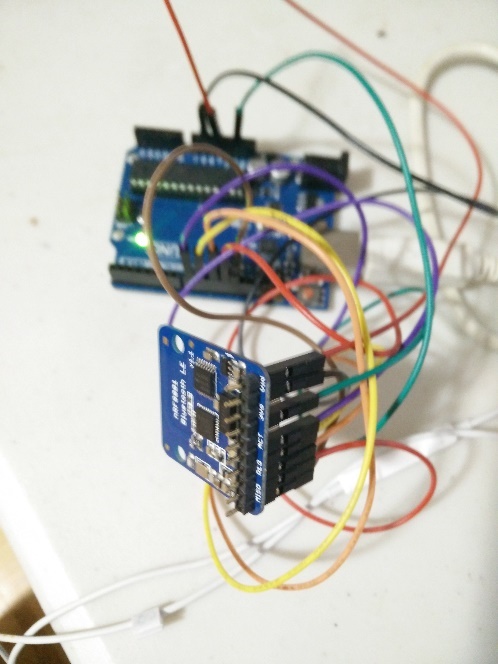
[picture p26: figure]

## The Relays Circuit

You may decide to have a portion of your circuitry printed (in which case you would want to print the file PCB V7.brd or you may choose to solder everything in which case you will need a perf board.

### Soldering onto the Perf Board:

You will need to solder the items mentioned on the Simplified Electronics Parts List so that you produce this circuit:


### Printing your Own PCB

To print your own PCB, use the PCB V7.brd file in Simplified Schematic. If you are using an Arduino UNO board (Option A or B), you should not solder the following components onto the PCB.

- DC JACK
- Diode D1
- Capacitors C1, C2, C3, C4
- ATMEGA328P IC1
- Voltage Regulator 7805T IC2
- Quartz Crystal 16MHZ Q1


If you are using the entire board with the built in Arduino UNO chip (Option C), then you must solder everything. The Atmega328p chip will need to programmed the Arduino Bootloader onto it before you can upload the Arduino Code onto it. There are a number of ways on the internet which show how to program Atmel328p chips with the Arduino Bootloader. For example, you can use the AVR ISP MKII from Atmel. Choose whatever method you are comfortable with. You can also purchase an Atmega328p chip that comes with the Arduino bootloader already on it.

## Pinout for Relays, Push Buttons, LEDs and Slide Switch


The Relays and LEDs are operated by output pins and the Push Buttons are operated by input pins.

The following table shows which pin corresponds to what function in the Arduino code “ConnectedCar” and “ConnectedCarTest”. Solder these connections or use header pins from the Arduino to the relay circuit board.

Output pins

Component | Function | Pin Number
Relays | Garage Stop | 7
| Garage Open | 4
| Garage Close | 5
| Lights On/Off | 10
LEDs | LED: Red | 3
| LED: Green | A5
| LED: Yellow | 2

Input pins

Component | Function | Pin Number
Push Button | Garage Stop | A0
| Garage Open | A1
| Garage Close | A2
| Lights On/Off | A3
| Bluetooth Unlock | A4
Slide Switch | Disable Bluetooth | This switch must be on the 5V wire connection between the Arduino and the Bluetooth Low Energy Chip. Hence, “Disable Bluetooth” turns of the power itself to the Bluetooth Chip.

If you are going ahead with Option C and are having trouble identifying which pin on the Atmega328p corresponds which pin number, use this diagram below:


## Final Steps:

Connect wires from pre-existing garage door openers into the terminal blocks. Refer to the Garage Door Openers on Market (Manuals) folder to get an idea of how majority of the garage door openers on the market work. Do the same for lights. As this involves working with the mains, this task must be carried out with the aid of a professional certified electrician.

Connect the 5V dc jack onto the Arduino to power it. You can now insert the electronics into the GateBox panel and close the seal to power it up.

Your GateBox panel is now ready.

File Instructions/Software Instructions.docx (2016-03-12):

# GATEBOX: SOFTWARE INSTRCUTIONS

By Shafeeq Rabbani


## GATT PROFILE

It is essential that in order to fully understand this project, you study what is GATT profile. GATT profile, short for Generic Attribute Profile, sits on top of the attribute profile. It is used in Bluetooth Low Energy. Look at the image below to get an idea of the

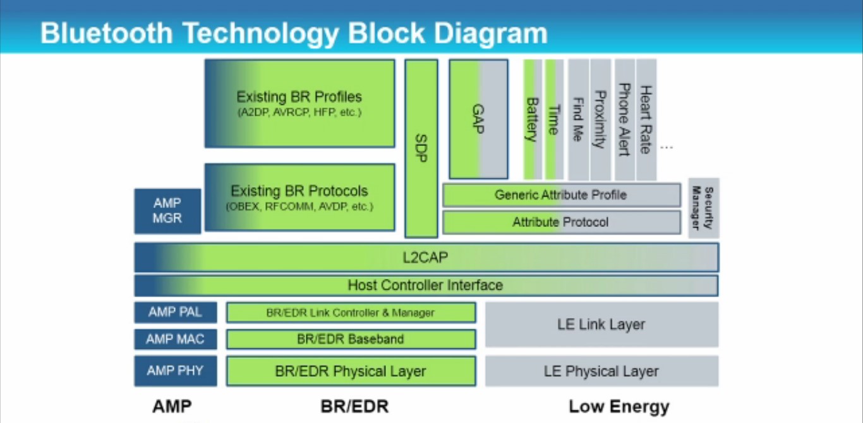
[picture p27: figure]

Much like how BACnet BIBBs contain properties, GATT characteristics contain properties. Look at the diagram below for a broad understanding of the GATT structure.

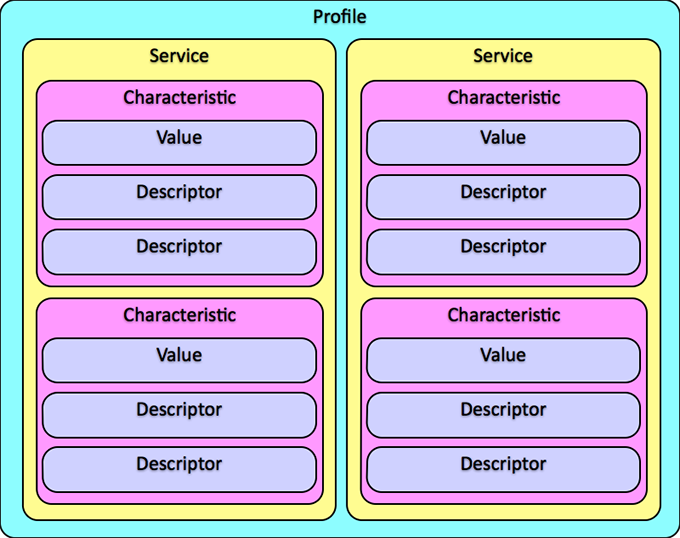
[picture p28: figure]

## nRFgo STUDIO

NOTE: if you don’t want to use nRFgo STUDIO, you can simply use the services.h file already created for you found with the Arduino code.

In the GATT Profile, Services and Characteristics are described by what is called the UUID (Universally Unique Identifiers). We made custom UUIDs:

Table A:

Service Name | UUID
ConnectedCar | CC01

Table B:

Characteristic Name | UUID | Possible data accepted | Max data length
Password | CC02 | 4-digit decimal number | 2
changePassword | CC03 | 4-digit decimal number | 2
Result | CC04 | 1-digit decimal number (1 or 0) | 1
changeResult | CC05 | 1-digit decimal number (1 or 0) | 1
lightsOn | CC06 | 1-digit decimal number (1 or 2) | 1
garageDoor | CC07 | 1-digit decimal number (1,2 or 3) | 1

You will have to build a GATT structure as described above. Different manufacturers have different software applications you can use to build your custom GATT structure. As we are using the nRF8001 chip, we will use the software that comes with it, nRFgo Studio. This software can be downloaded from the internet for free from: https://www.nordicsemi.com/eng/Products/2.4GHz-RF/nRFgo-Starter-Kit or you can extract it from the zip file in the “Software Needed” folder. While installing this software onto your computer, make sure to select the 32/64-bit version as per your operating system.

To make your GATT structure, click file → new → nRF8001.

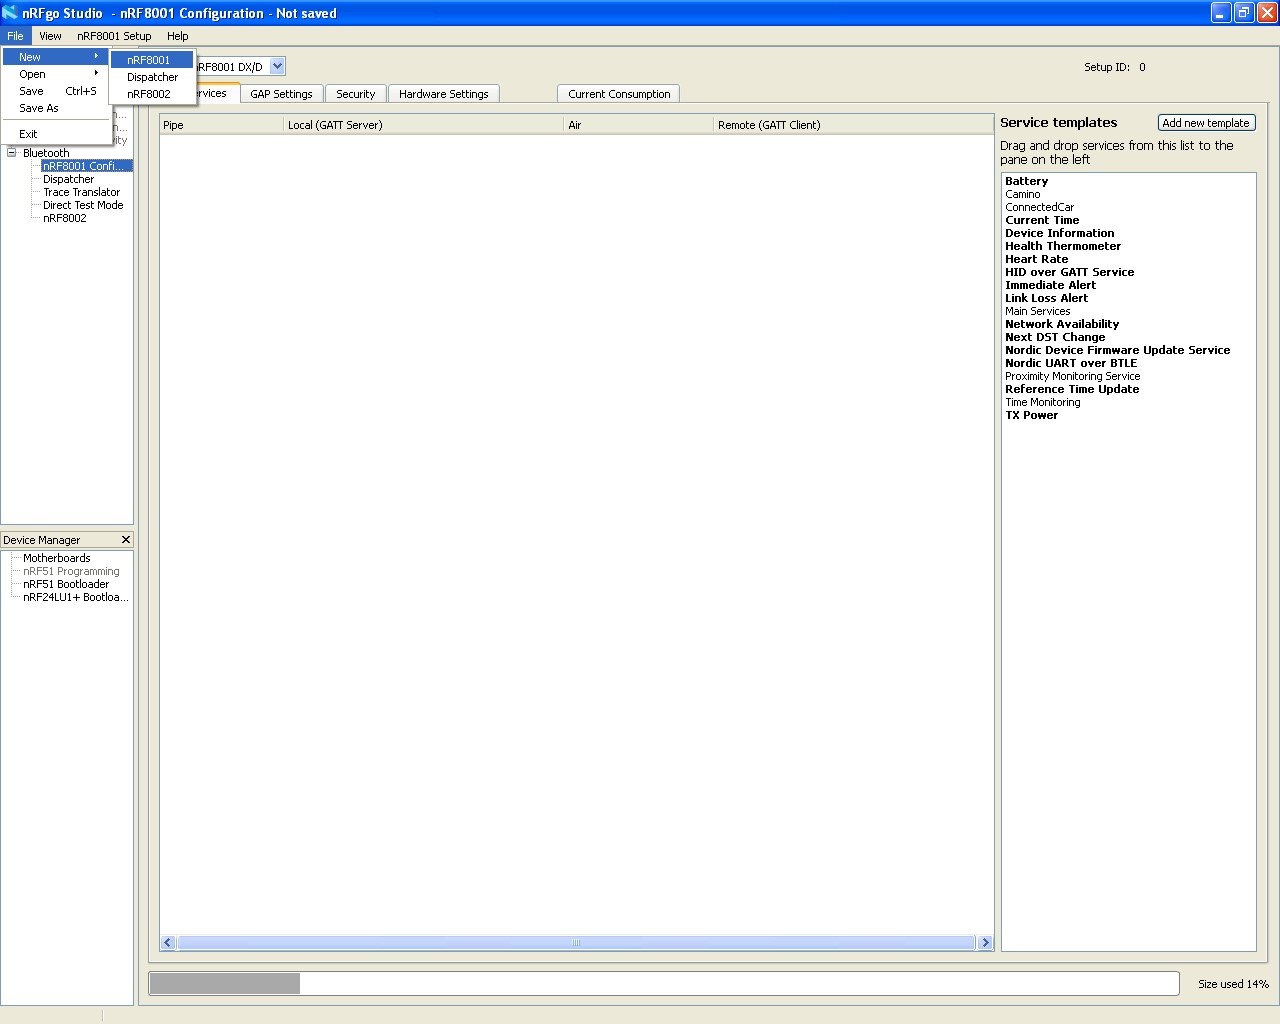
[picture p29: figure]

Name the service and give it a UUID (Refer to Table A). UUID is in hexadecimal format.

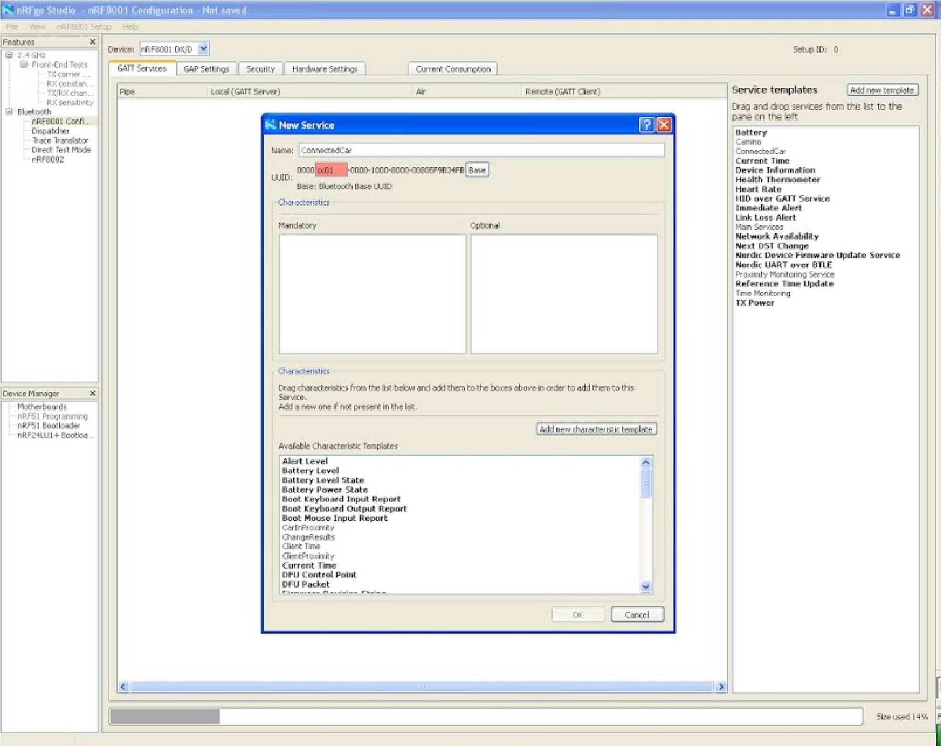
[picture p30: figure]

Click add new characteristic template. Name the characteristic, and the UUID associated with it and the byte. Initial value must be set to 0. Refer to Table B for the name, UUID and max data length of each characteristic.

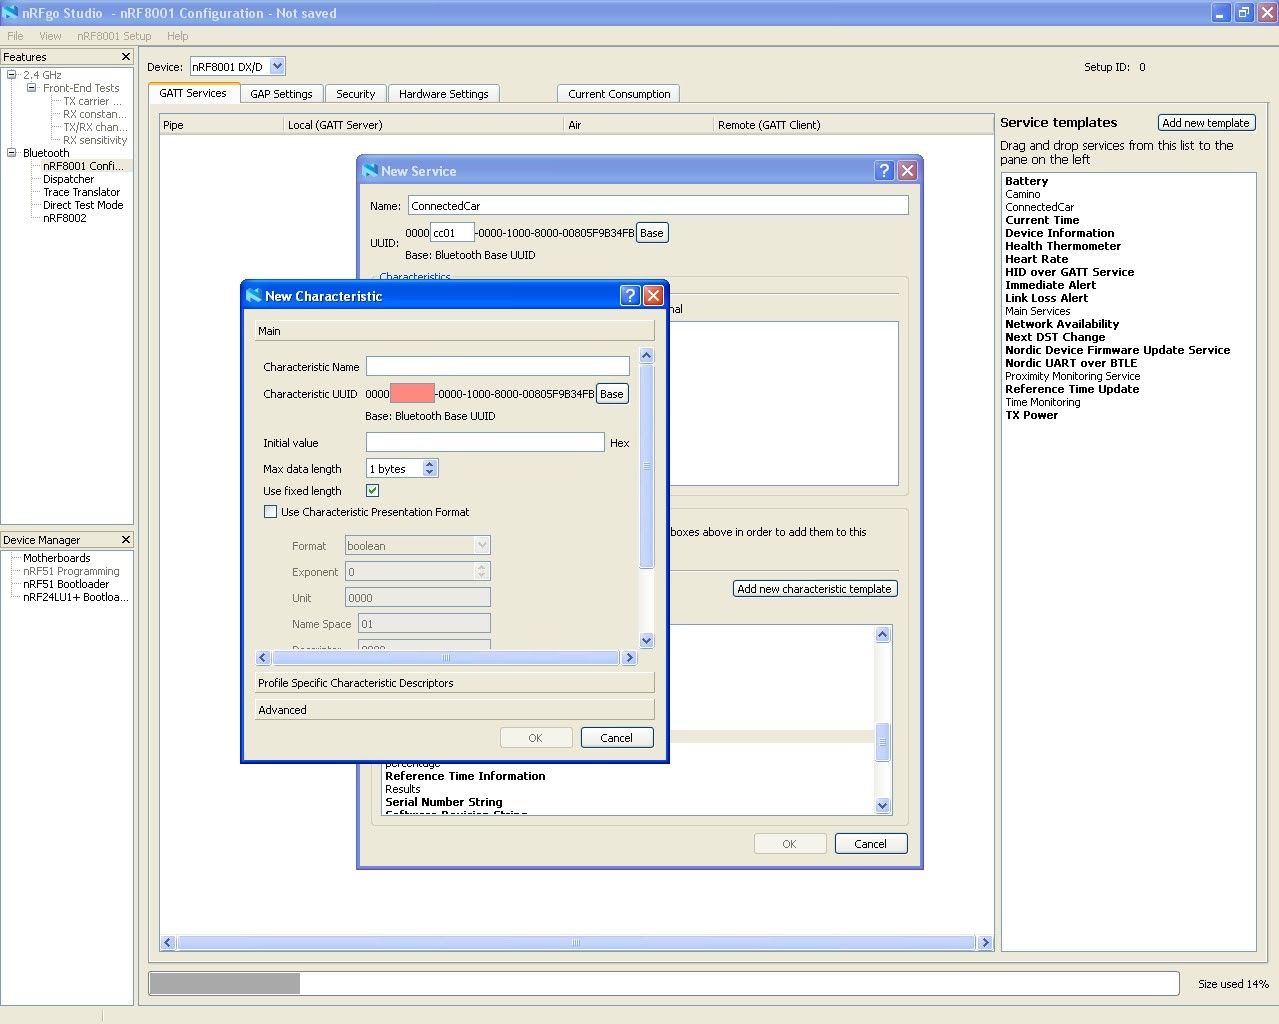
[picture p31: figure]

Click on profile specific characteristic descriptors and select Notify and Write without response.

(NOTE: Indicate is like Notify except with acknowledgement. Working with acknowledgement data is very complex and it is recommended that you avoid using it for now).

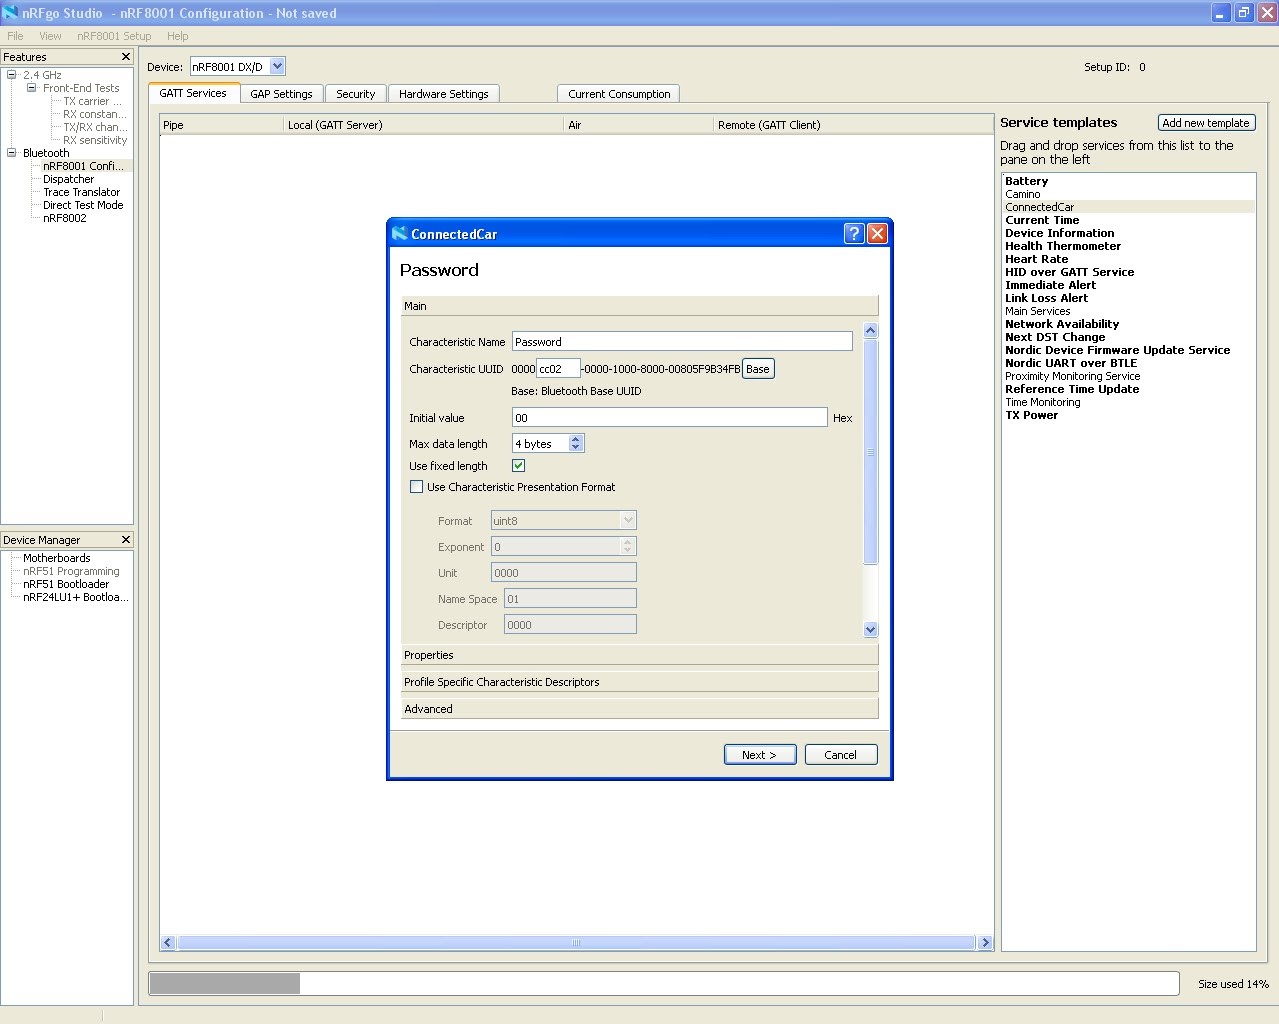
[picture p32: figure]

Click next and when the pop up window disappears, click and drag ConnectedCar under GATT server.

You should create all characteristics necessary so that your final window looks like this when you drag it. Refer to table A for characteristic codes.

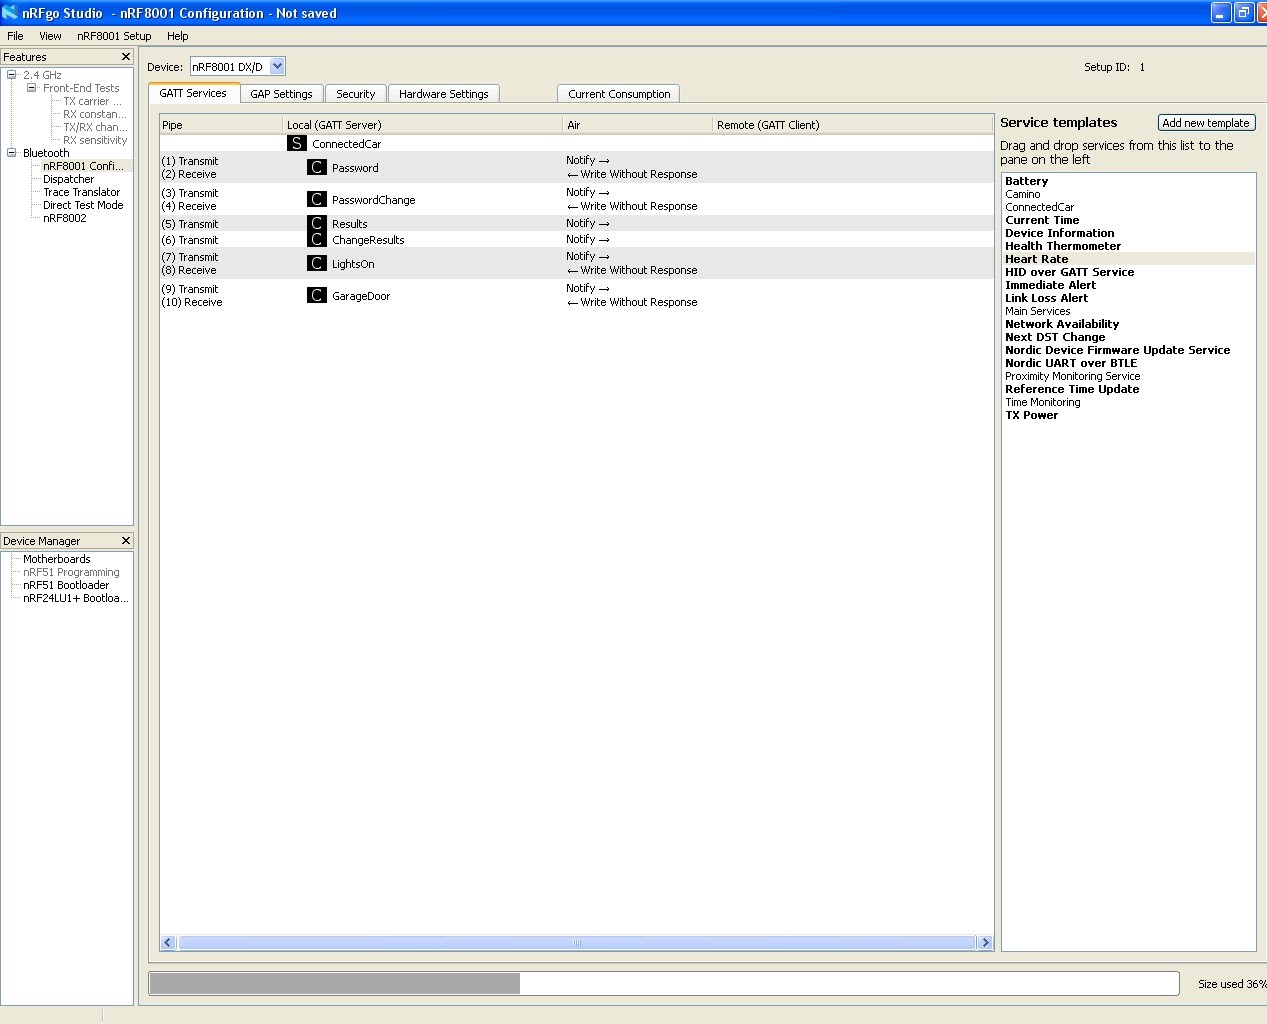
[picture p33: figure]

Click on GAP Settings.

Under service solicitation and local services, put the checkbox on the GATT server.

Click on ACI Connect, from the drop down menu select Use Complete and click the checkbox on local services (GATT server). Do the same for ACI Bond and ACI Broadcast.

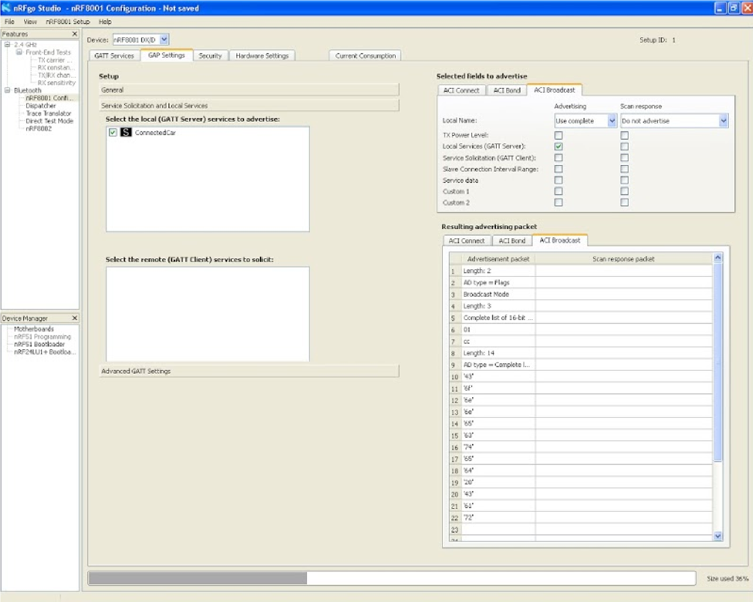
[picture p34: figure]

Go to GAP Settings -> Add Service Changed Characteristic. This feature is useful if you are making your custom services and characteristics. Sometimes what tends to happen is that the older version of services and characteristics that you make are stored in the cache of your smartphone and are not overwritten even if you recompiled a different version of the services.h file onto the GATT server (the Arduino board is our GATT server). Service Changed Characteristic will allow the client to do service discovery every time it connects to the server.

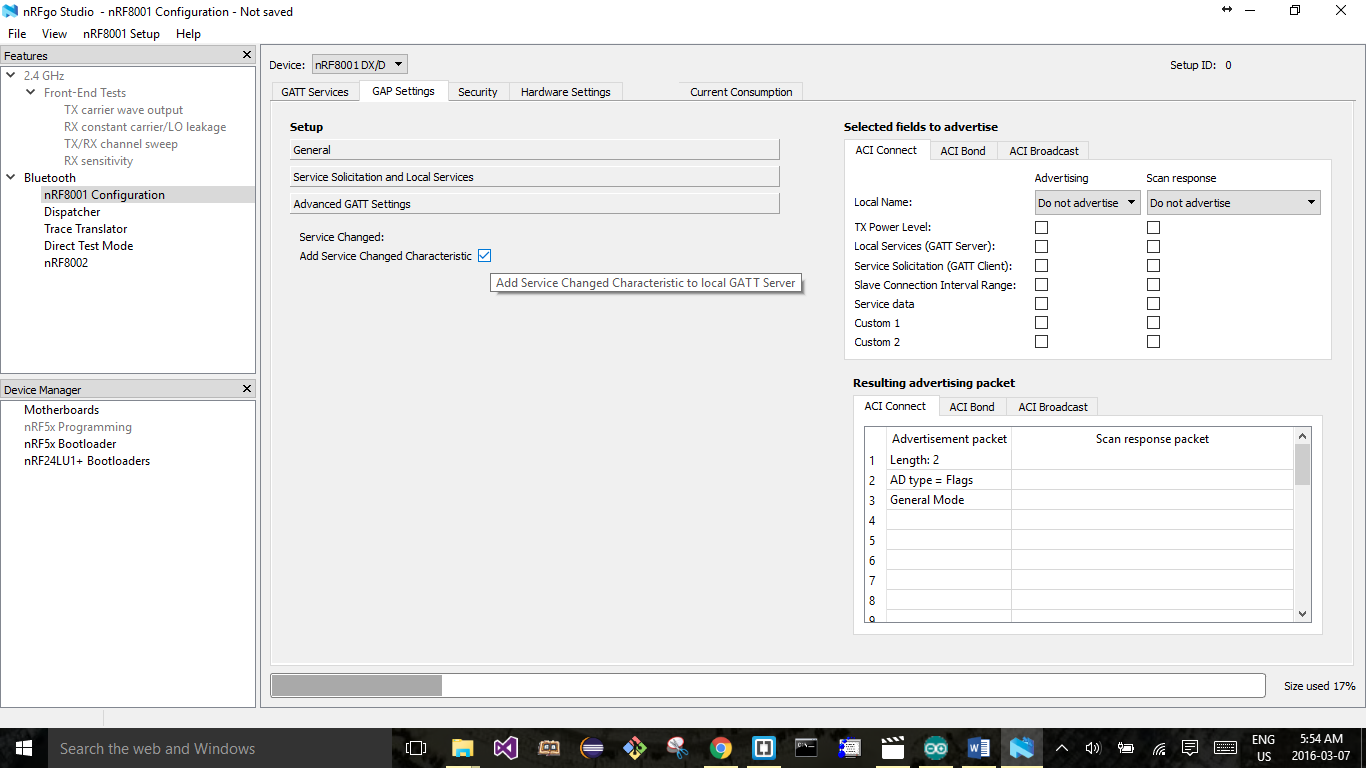
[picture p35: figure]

Click on nRF8001 setup → generate source files → generate only services.h.

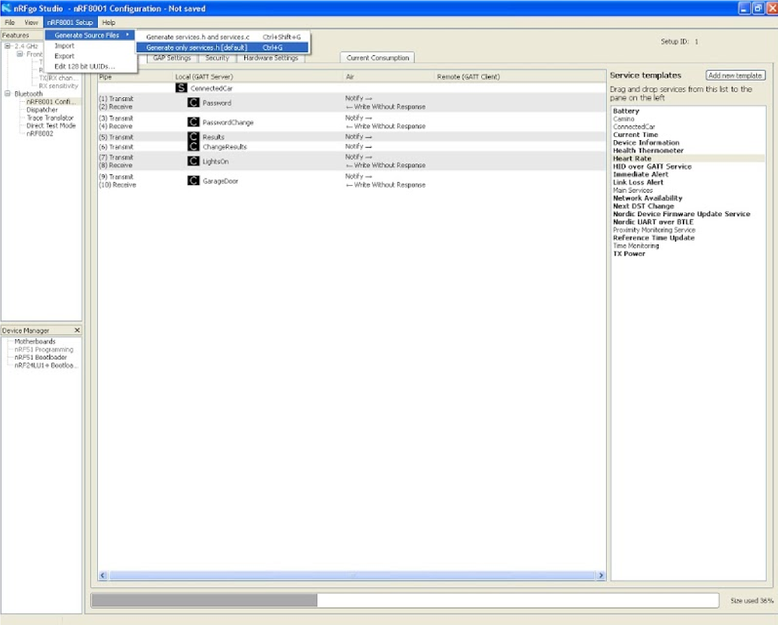
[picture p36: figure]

This will generate two files. services_lock.h and services.h. Do not use services_lock.h. This will permanently write to your UUIDs to nRF8001 chip. From then on, the services and characteristics nRF8001 chip cannot be changed. The Arduino code already has #include "services.h".

## Download and Install Arduino IDE version 1.0.6

You must use version 1.0.6 because the code will not compile on later versions of the IDE. You can download this from the Arduino website or extract it from the GitHub folder “Software Needed”.

Special note for detailed list: If your ATMEGA328p chip does not have the Arduino bootloader on it, then the bootloader must be uploaded onto the chip. There are various methods on the internet that show how to upload the Arduino bootloader onto an ATMEGA328p chip (For example, using the AVR ISP MKII). You can choose any method. You could also purchase an ATMEGA328p chip with the Arduino bootloader already onto it.

## Install BLE and Time Library

If you have used Arduino IDE in the past, you would know how to add external libraries into the Arduino. Add the BLE library and Time Library.

## Test the Arduino Code

In order to make sure your Bluetooth chip is working properly and that your wiring is correct compile and upload the ConnectedCarTest code into the Arduino UNO. The only difference between ConnectedCarTest and ConnectedCar is the fact that ConnectedCarTest has all the pins (except for digital pin 6) commented out. As initially you don’t have all your hardware relays and pull up and pull down resistors connected, the voltage at a certain pin can fluctuate creating values that fill flood the serial monitor. This will make it difficult for you to test your code.

A good way to test if your UUIDs are working correctly is by an app on the apple app store called “LightBue Explorer – Bluetooth Low Energy” By Punch Through. This app is free to download. It will allow you to send specific values to a UUID. You can also test directly with the Windows Smartphone Application (which you would use).

Open the Serial monitor. If it asks you to remove pin 6 and reset, keep on resetting until the device is ‘active’.

Open the app (while the serial monitor of the Arduino IDE is turned on) and enter UUID CC02. Enter 0000. It this password is correct (as in the EEPROM address bits 1000 to 1003) it will say “correct password”. If it is incorrect, it will say “incorrect password, 2 tries remaining”. It will also tell you what password is stored in the EEPROM. Enter this password into your favorite Decimal to Hexadecimal converter online to get the four-digit Hexadecimal code. This four-digit Hexadecimal code must then be written to CC02.

Note: if you decide to make your own customized GATT services and characteristics and find that the LightBlue app is showing an older version services and characteristics you made, simply turn off your Bluetooth and turn it on again. This will result in the phone getting rid of its Bluetooth cache and make a fresh start with service discovery of the GATT server.

## Changing the password

Think of a four digit-number, insert it into your favorite Hexadecimal to Decimal converter online to get the hexadecimal code. Enter this hexadecimal code in characteristic CC03. (Make sure that you are still logged in).

Upload the ConnectedCar code onto the Arduino and wire up the electronics.

The board is now ready to serve as the GateBox.

## Interesting facts

If you press get notifications after entering a password for login (in CC02) or a password for change (in CC03), you will see that a notification of 0000 is received. This is done in order to erase the password value on the characteristic. The Windows Smartphone application will do this automatically.

Light states: writing a value of 1 means OFF, writing a value of 2 means ON.

Garage door states: writing a value of 1 means STOP, writing a value of 2 means OPEN and writing a value of 3 means CLOSE.

In the case of light (CC06) and garage (CC07) states, if you press notification, the updated value of the garage door / light state appears. This is used by the Windows Smartphone Application as a confirmation as to what is the current state of the garage door / lights. When the user first logs in, the current value of the garage door and light are waiting as notifications to be sent to the smartphone. Remember: the states of garage door and light can change from the GateBox panel and hence the smartphone app must be updated on the latest states of the light and garage door every time it logs into the GateBox panel.

## Smartphone Application

There is a Windows App included into the folder “Windows Phone Application” that can be used. Currently, it is not on the Windows Store. Hence, it must be complied in visual studio and uploaded into a Windows Phone. It will have to be a Windows Phone and not an emulator. Overwhelming majority of phones today come with Bluetooth LE. However, it would be nice just to make sure that the phone of your choosing is compatible.

Anyone who follows the documentation for making Bluetooth Low Energy apps on Windows/Android/iPhone/Blackberry, you can easily make your own version of the app for this project. It would be nice to have different versions of the app available on their respective application markets and stores from where users can download these apps ready to use in this project.

## Mirroring the Smartphone Application

For the purposes of demonstration, an e3iO Car PC was used http://e3io.com/2din-car-pc-small-edition. This Car PC runs Windows 8 – it is basically a PC in your car. Any number of software applications was used to mirror the smartphone’s screen onto the Car PC. They can be downloaded from the internet for free. One such application is Car Dash (https://www.microsoft.com/en-us/store/apps/car-dash/9wzdncrfj0b9).

Getting an application into an auto manufacturer’s dashboard requires overcoming a lot of regulations and cost a lot of money for testing. Services that make it possible for smartphone applications to be mirrored into the car’s dashboard are:

1. AndroidAuto by Google
2. Apple CarPlay by Apple
3. MirrorLink by Car Connectivity Consortium
4. AppLink by Ford

An app that has undergone testing for one of the services above will only run on that service. Which means that if you want to run your application on AppLink and MirrorLink, you will have to pay the testing fee for AppLink and separate testing fee for MirrorLink. This investment would be preferable to someone interested in developing this further and manufacturing it into a commercial product.

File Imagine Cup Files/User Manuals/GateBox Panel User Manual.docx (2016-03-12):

# GATEBOX: PANEL USER MANUAL

By Shafeeq Rabbani


Green indicates Smartphone is connected to panel.

Yellow indicates panel is locked out.

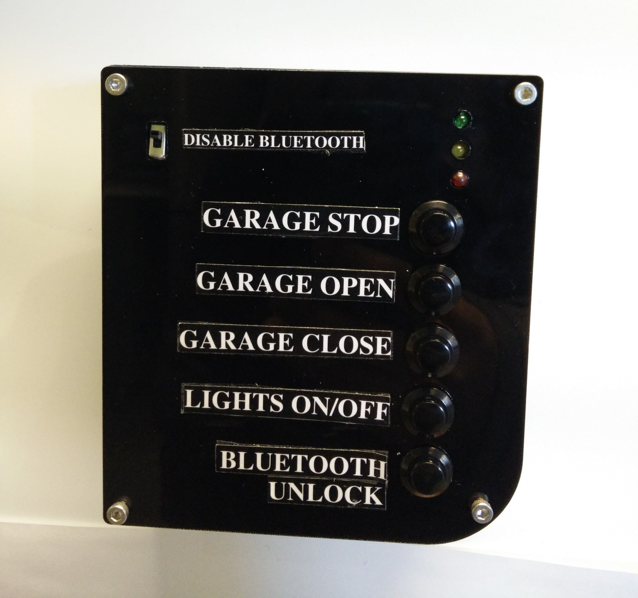
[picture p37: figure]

Red indicates no smartphone is connected to panel.

This button turns off the Bluetooth device. This feature is useful in the situation where the user is going on a vacation and does not want the GateBox panel’s Bluetooth login feature running during this time.

After 3 incorrect password attempts, the user is locked-out. The only way to reactivate wireless operation is by manually pressing the Bluetooth Unlock button.

Turn the lights On/Off

Close the Garage Door

Open the Garage Door

Stop the Garage Door

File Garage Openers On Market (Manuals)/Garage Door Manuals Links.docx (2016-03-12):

http://www.manualslib.com/manual/603400/Liftmaster-412hm.html

http://www.manualslib.com/manual/442885/Liftmaster-850lm.html#manual

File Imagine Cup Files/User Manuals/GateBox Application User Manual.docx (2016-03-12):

GATEBOX Application

# User’s Manual Guide

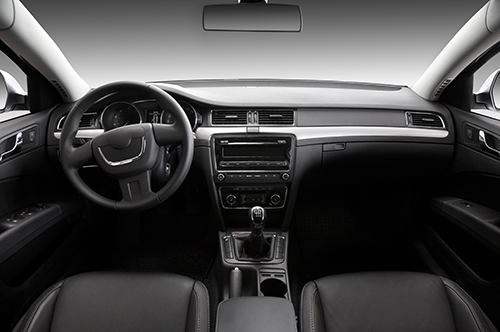
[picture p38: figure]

# Installation/ Configuration

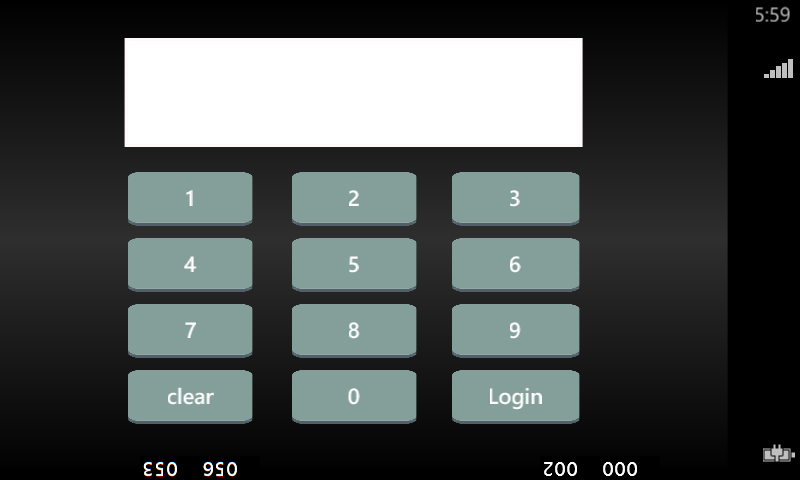
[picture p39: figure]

The GATEBOX application is easy and simple to use. In order to use your GATEBOX, you will have to download the app from the Windows Store.

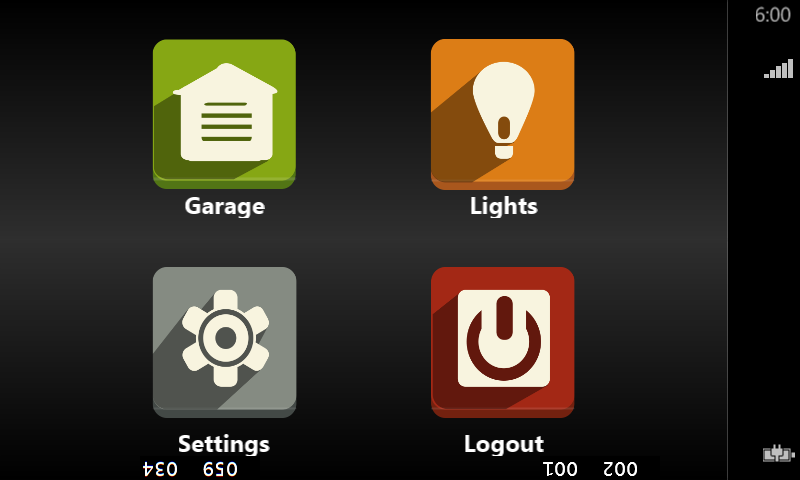
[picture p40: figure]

Once downloaded, launch the application to connect the GATEBOX. The default password on the application is 0000. It is recommended that you change the password once logged it.

The home menu consists of garage, lights, settings and logout.

# Garage

In the garage door section of the application (), you can control your garage door using the GATEBOX.

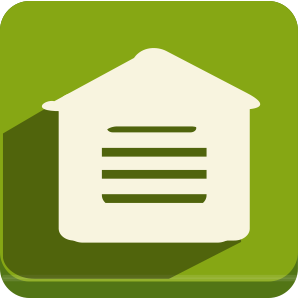
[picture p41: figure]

## Opening /Closing / Stopping garage door

1. If not logged in already, log into the GATEBOX application.
2. Click on the garage icon .
- To open the garage door click on the open icon.
- To stop the garage door, click on the top icon.
- To close the garage door, click on the close icon.

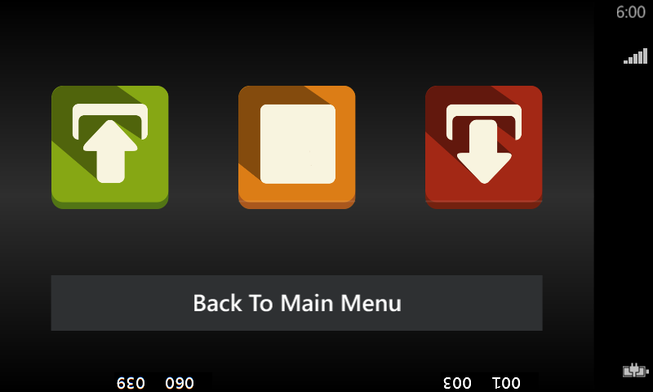
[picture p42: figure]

3. Click back to menu once finish.

# Lights

In the lights section of the application (), you can control your house lights using the GATEBOX.

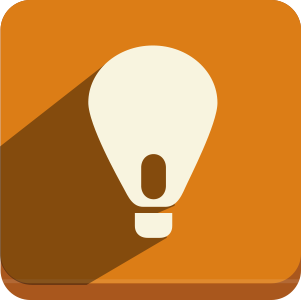
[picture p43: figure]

## Switching on/off lights

1. If not logged in already, log into the GATEBOX application.
2. Click on the lights icon .
- To switch on the lights click the on icon.

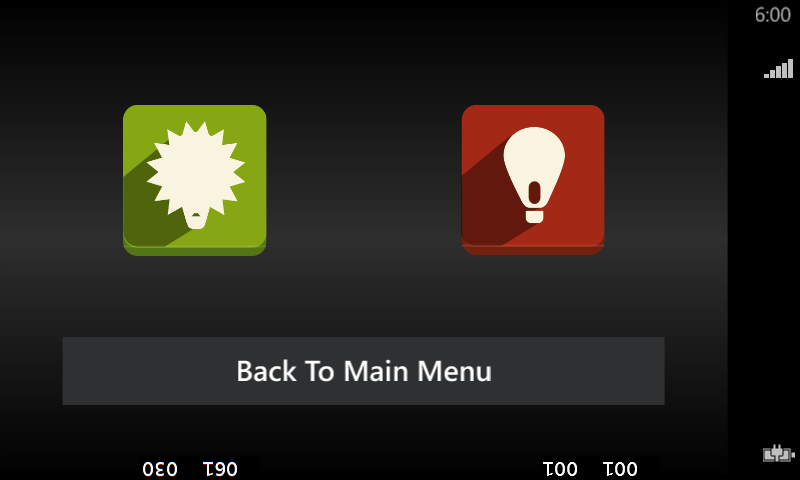
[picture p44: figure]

- To switch off the lights, click the off close icon.
4. Click back to menu once finish.

# Settings

In the settings section of the application (), you can change your current password for the GATEBOX.

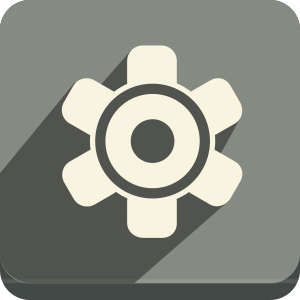
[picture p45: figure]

## Changing your password

1. Log into the GATEBOX application.
2. Click on the settings icon .
3. Select change password.
4. Enter the old password.

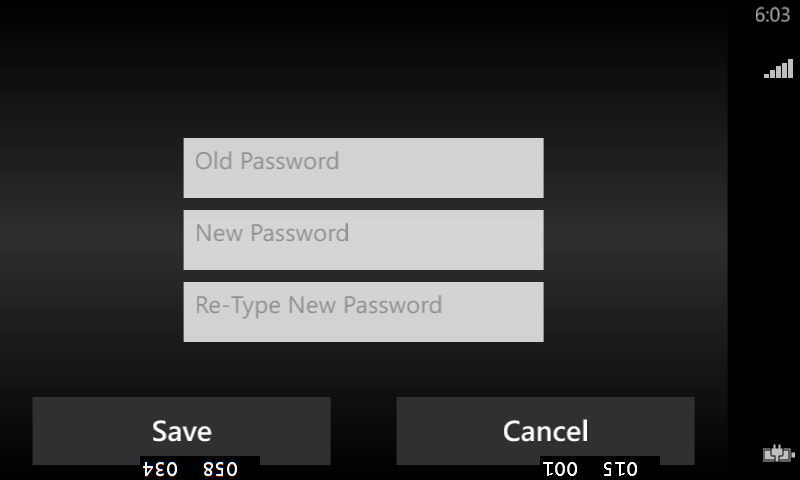
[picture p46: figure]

5. Enter the new password.
6. Re-type the new password in again and click save.

GateBox / Use’s Manuel Guide 6

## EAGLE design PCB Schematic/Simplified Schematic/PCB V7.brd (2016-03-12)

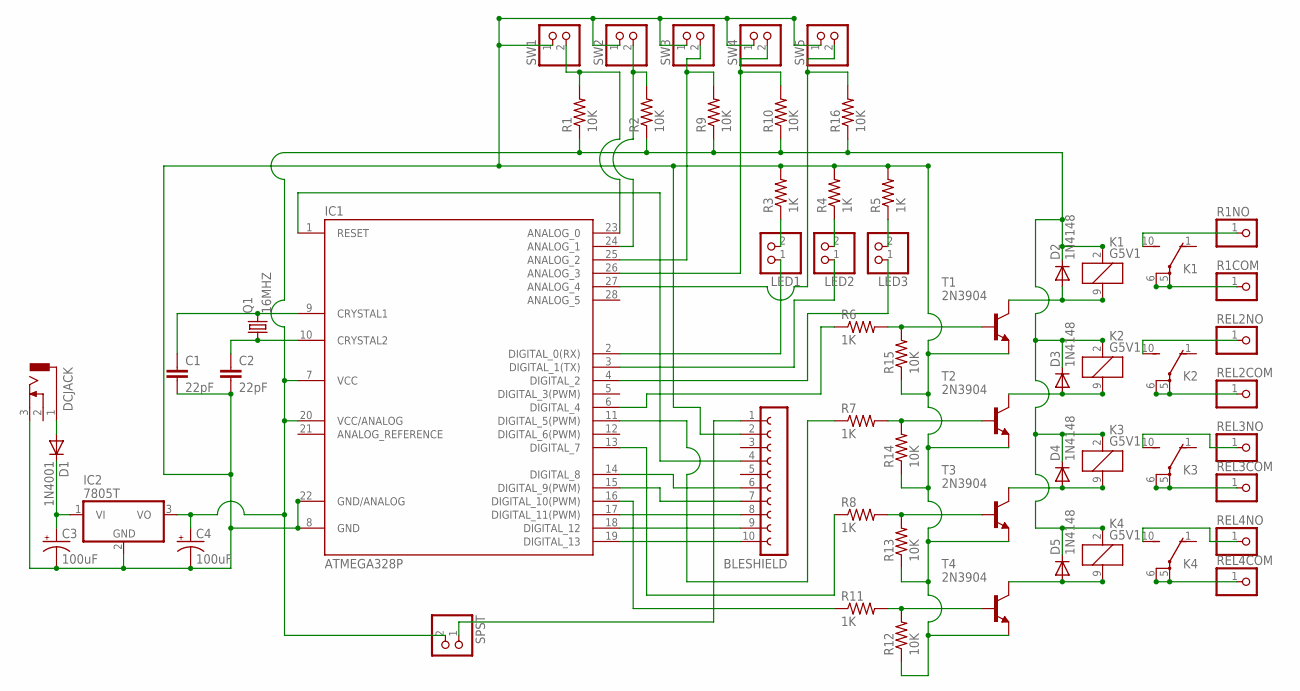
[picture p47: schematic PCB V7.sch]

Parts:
BLESHIELD: FE10-1; FE10
C1, C2: 22pF; C025-030X050
C3, C4: 100uF; E2,5-6
D1: 1N4001; DO41-10
D2, D3, D4, D5: 1N4148; DO35-7
DCJACK: DCJ0202
IC1: ATMEGA328P; DIL28-3
IC2: 7805T; TO220H
K1, K2, K3, K4: G5V1
LED1, LED2, LED3: PINHD-1X2; 1X02
Q1: 16MHZ; HC49/S
R1, R2, R9, R10, R12, R13, R14, R15, R16: 10K; 0204/5
R1COM, R1NO: PINHD-1X1; 1X01
R3, R4, R5, R6, R7, R8, R11: 1K; 0204/5
REL2COM, REL2NO, REL3COM, REL3NO, REL4COM, REL4NO: PINHD-1X1; 1X01
SPST: PINHD-1X2; 1X02
SW1, SW2, SW3, SW4, SW5: PINHD-1X2; 1X02
T1, T2, T3, T4: 2N3904; TO92

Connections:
GND: BLESHIELD.2, C1.2, C2.2, C3.-, C4.-, DCJACK.3, IC1.8 (GND), IC1.22 (GND/ANALOG), IC2.2 (GND), R3.2, R4.2, R5.2, R12.1, R13.1, R14.1, R15.1, SW1.1, SW2.1, SW3.1, SW4.1, SW5.1, T1.3 (E), T2.3 (E), T3.3 (E), T4.3 (E)
unnamed: BLESHIELD.10, IC1.19 (DIGITAL_13)
unnamed: R6.2, R15.2, T1.2 (B)
unnamed: IC1.3 (DIGITAL_1(TX)), LED2.1
unnamed: BLESHIELD.6, IC1.14 (DIGITAL_8)
unnamed: C1.1, IC1.9 (CRYSTAL1), Q1.2
unnamed: C2.1, IC1.10 (CRYSTAL2), Q1.1
unnamed: IC1.24 (ANALOG_1), R2.2, SW2.2
unnamed: C3.+, D1.C, IC2.1 (VI)
unnamed: BLESHIELD.4, IC1.1 (RESET)
unnamed: BLESHIELD.7, IC1.15 (DIGITAL_9(PWM))
unnamed: BLESHIELD.8, IC1.17 (DIGITAL_11(PWM))
unnamed: BLESHIELD.9, IC1.18 (DIGITAL_12)
unnamed: D3.A, K2.9 (2), T2.1 (C)
unnamed: R7.2, R14.2, T2.2 (B)
unnamed: IC1.23 (ANALOG_0), R1.2, SW1.2
unnamed: D2.A, K1.9 (2), T1.1 (C)
unnamed: LED1.2, R3.1
unnamed: LED2.2, R4.1
unnamed: LED3.2, R5.1
unnamed: C4.+, D2.C, D3.C, D4.C, D5.C, IC1.7 (VCC), IC1.20 (VCC/ANALOG), IC2.3 (VO), K1.2 (1), K2.2 (1), K3.2 (1), K4.2 (1), R1.1, R2.1, R9.1, R10.1, R16.1, SPST.2
unnamed: IC1.27 (ANALOG_4), R16.2, SW5.2
unnamed: K1.5, K1.6, R1COM.1
unnamed: K1.10 (S), R1NO.1
unnamed: IC1.16 (DIGITAL_10(PWM)), R11.1
unnamed: IC1.25 (ANALOG_2), R9.2, SW3.2
unnamed: IC1.6 (DIGITAL_4), R6.1
unnamed: D1.A, DCJACK.1
unnamed: IC1.26 (ANALOG_3), R10.2, SW4.2
unnamed: IC1.2 (DIGITAL_0(RX)), LED1.1
unnamed: BLESHIELD.1, SPST.1
unnamed: K2.10 (S), REL2NO.1
unnamed: K2.5, K2.6, REL2COM.1
unnamed: K3.5, K3.6, REL3COM.1
unnamed: IC1.13 (DIGITAL_7), R8.1
unnamed: IC1.11 (DIGITAL_5(PWM)), R7.1
unnamed: K3.10 (S), REL3NO.1
unnamed: K4.10 (S), REL4NO.1
unnamed: K4.5, K4.6, REL4COM.1
unnamed: R8.2, R13.2, T3.2 (B)
unnamed: IC1.4 (DIGITAL_2), LED3.1
unnamed: D4.A, K3.9 (2), T3.1 (C)
unnamed: R11.2, R12.2, T4.2 (B)
unnamed: D5.A, K4.9 (2), T4.1 (C)

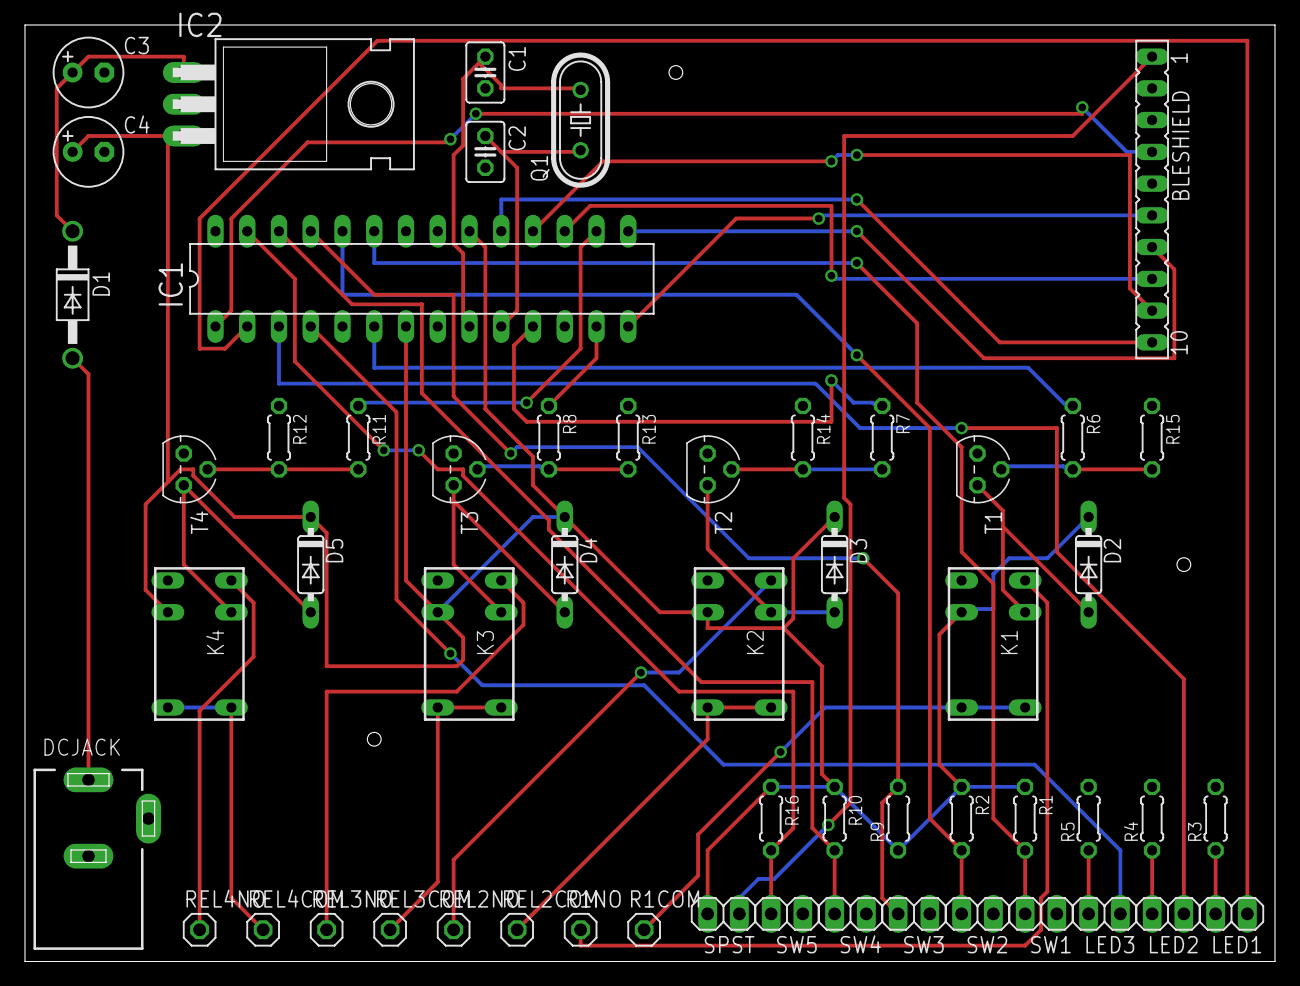
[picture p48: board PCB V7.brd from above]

Board: 2 copper layers, 100.0 x 74.9 mm, 55 parts (0 on the bottom side), 44 nets.

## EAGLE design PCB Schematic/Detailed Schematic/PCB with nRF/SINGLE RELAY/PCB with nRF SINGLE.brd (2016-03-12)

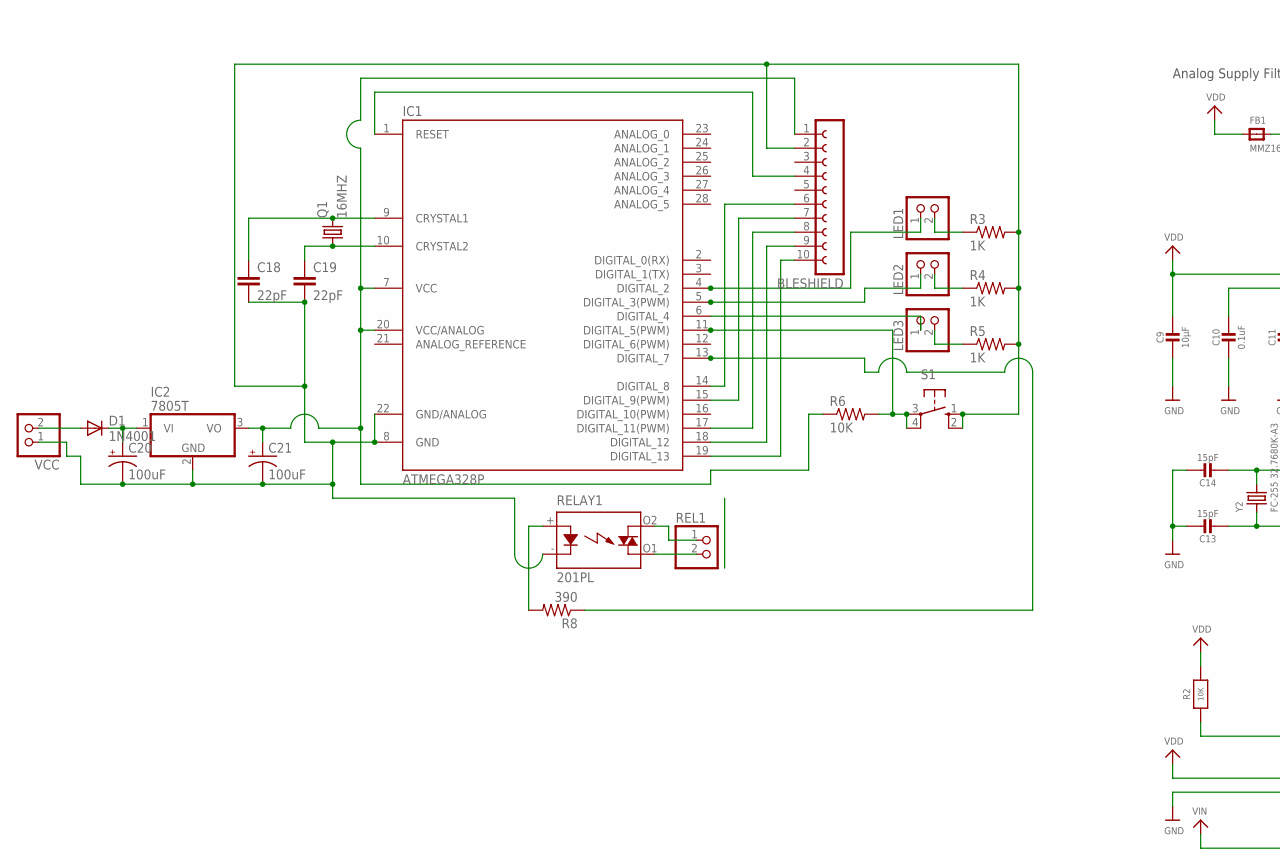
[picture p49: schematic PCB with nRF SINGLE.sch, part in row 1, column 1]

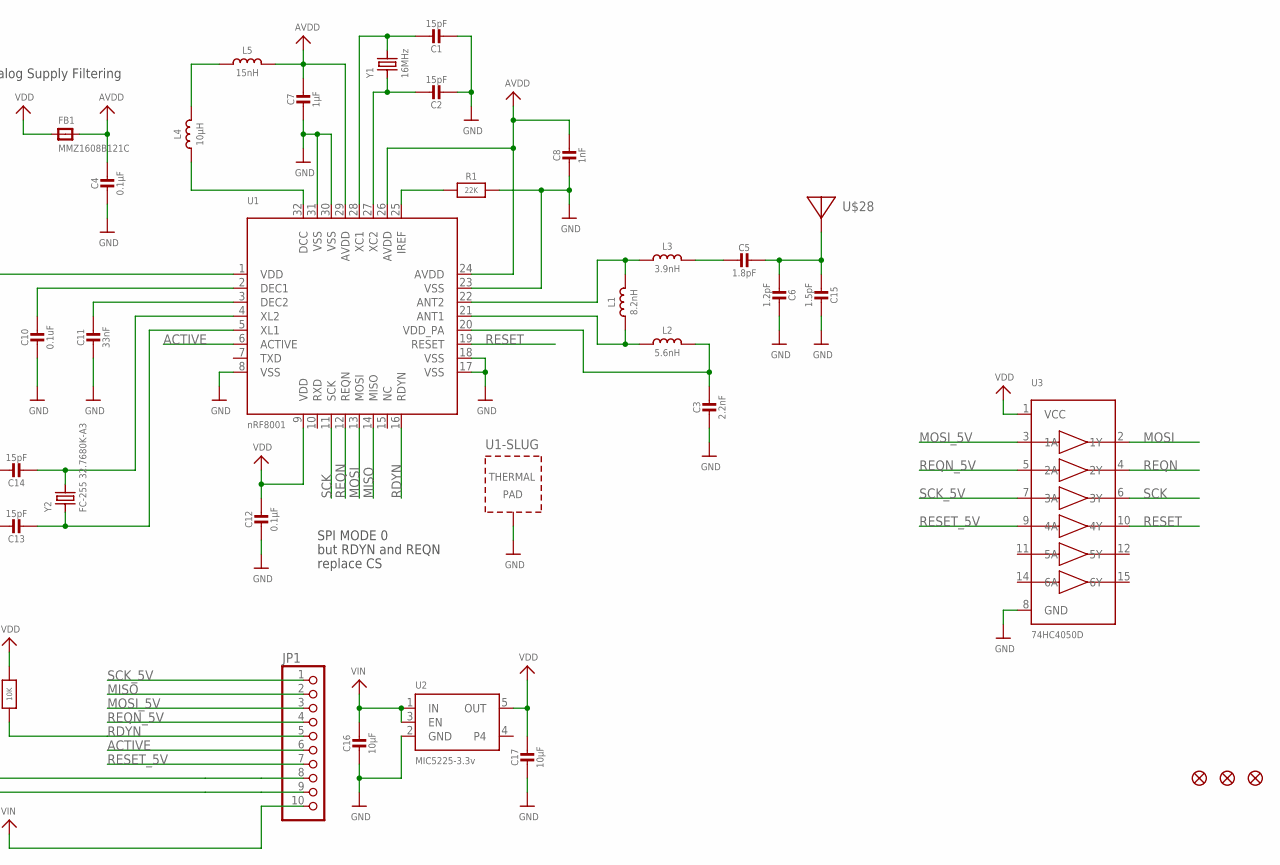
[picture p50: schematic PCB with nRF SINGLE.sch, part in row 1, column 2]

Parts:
BLESHIELD: FE10-1; FE10
C1, C2, C13, C14: 15pF; 0805-NO
C3: 2.2nF; _0402
C4, C12: 0.1µF; 0805-NO
C5: 1.8pF; _0402MP
C6: 1.2pF; _0402MP
C7: 1µF; 0805-NO
C8: 1nF; _0603
C9, C16, C17: 10µF; 0805-NO
C10: 0.1uF; 0805-NO
C11: 33nF; 0805-NO
C15: 1.5pF; _0402MP
C18, C19: 22pF; C025-030X050
C20, C21: 100uF; E2,5-6
D1: 1N4001; DO41-10
FB1: MMZ1608B121C; 0805
FID1, FID2, FID3: FIDUCIAL""; FIDUCIAL_1MM
IC1: ATMEGA328P; DIL28-3
IC2: 7805T; TO220H
JP1: HEADER-1X1070MIL; 1X10_ROUND70
L1: 8.2nH; _0402
L2: 5.6nH; _0402
L3: 3.9nH; _0402
L4: 10µH; _0603
L5: 15nH; _0603
LED1, LED2, LED3: PINHD-1X2; 1X02
Q1: 16MHZ; HC49/S
R1: 22K; _0805MP
R2: 10K; 0805-NO
R3, R4, R5: 1K; 0204/5
R6: 10K; 0204/5
R8: 390; 0204/5
REL1: PINHD-1X2; 1X02
RELAY1: 201PL; AQG
S1: 10-XX; B3F-10XX
U1: nRF8001; QFN32_5MM
U2: MIC5225-3.3v; SOT23-5
U3: 74HC4050D; TSSOP16
U$28: ANTENNA_PCBNRF8001_1.6MM; ANT_PCB_2.4GHZ_NRF8001_1.6MM_1OZ
VCC: PINHD-1X2; 1X02
Y1: 16MHz; CRYSTAL_2.5X2
Y2: FC-255 32.7680K-A3; CRYSTAL_4.9X1.8

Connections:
ACTIVE: JP1.6, U1.6 (ACTIVE)
AVDD: C4.1, C7.1, C8.1, FB1.2, L5.2, U1.24 (AVDD), U1.26 (AVDD), U1.29 (AVDD)
GND: C1.2, C2.2, C3.2, C4.2, C6.1, C7.2, C8.2, C9.2, C10.2, C11.2, C12.2, C13.1, C14.1, C15.1, C16.2, C17.2, JP1.9, R1.2, U1.8 (VSS), U1.17 (VSS), U1.18 (VSS), U1.23 (VSS), U1.30 (VSS), U1.31 (VSS), U1.33 (TP), U2.2 (GND), U3.8 (GND)
MISO: JP1.2, U1.14 (MISO)
MOSI: U1.13 (MOSI), U3.2 (1Y)
MOSI_5V: JP1.3, U3.3 (1A)
unnamed: BLESHIELD.10, IC1.19 (DIGITAL_13)
unnamed: L1.2, L3.1, U1.22 (ANT2)
unnamed: L1.1, L2.1, U1.21 (ANT1)
unnamed: C3.1, L2.2, U1.20 (VDD_PA)
unnamed: L4.2, L5.1
unnamed: C5.2, L3.2
unnamed: C11.1, U1.3 (DEC2)
unnamed: C10.1, U1.2 (DEC1)
unnamed: C1.1, U1.28 (XC1), Y1.3 (2)
unnamed: C2.1, U1.27 (XC2), Y1.1
unnamed: L4.1, U1.32 (DCC)
unnamed: R1.1, U1.25 (IREF)
unnamed: C5.1, C6.2, C15.2, U$28.FEED
unnamed: C18.1, IC1.9 (CRYSTAL1), Q1.2
unnamed: C19.1, IC1.10 (CRYSTAL2), Q1.1
unnamed: BLESHIELD.6, IC1.14 (DIGITAL_8)
unnamed: BLESHIELD.7, IC1.15 (DIGITAL_9(PWM))
unnamed: BLESHIELD.8, IC1.17 (DIGITAL_11(PWM))
unnamed: BLESHIELD.9, IC1.18 (DIGITAL_12)
unnamed: BLESHIELD.1, C21.+, IC1.7 (VCC), IC1.20 (VCC/ANALOG), IC2.3 (VO), R6.1
unnamed: BLESHIELD.4, IC1.1 (RESET)
unnamed: C14.2, U1.4 (XL2), Y2.2
unnamed: C13.2, U1.5 (XL1), Y2.1
unnamed: IC1.4 (DIGITAL_2), LED1.1
unnamed: IC1.5 (DIGITAL_3(PWM)), LED2.1
unnamed: LED1.2, R3.1
unnamed: LED2.2, R4.1
unnamed: LED3.2, R5.1
unnamed: IC1.11 (DIGITAL_5(PWM)), R6.2, S1.3, S1.4 (P1)
unnamed: REL1.2, RELAY1.O1 (DS2)
unnamed: IC1.13 (DIGITAL_7), R8.1
unnamed: C20.+, D1.C, IC2.1 (VI)
unnamed: BLESHIELD.2, C18.2, C19.2, C20.-, C21.-, IC1.8 (GND), IC1.22 (GND/ANALOG), IC2.2 (GND), R3.2, R4.2, R5.2, RELAY1.- (K), S1.1 (S), S1.2 (S1), VCC.1
unnamed: D1.A, VCC.2
unnamed: IC1.6 (DIGITAL_4), LED3.1
unnamed: R8.2, RELAY1.+ (A)
RDYN: JP1.5, R2.1, U1.16 (RDYN)
REL1: REL1.1, RELAY1.O2 (DS1)
REQN: U1.12 (REQN), U3.4 (2Y)
REQN_5V: JP1.4, U3.5 (2A)
RESET: U1.19 (RESET), U3.10 (4Y)
RESET_5V: JP1.7, U3.9 (4A)
SCK: U1.11 (SCK), U3.6 (3Y)
SCK_5V: JP1.1, U3.7 (3A)
VDD: C9.1, C12.1, C17.1, FB1.1, JP1.8, R2.2, U1.1 (VDD), U1.9 (VDD), U2.5 (OUT), U3.1 (VCC)
VIN: C16.1, JP1.10, U2.1 (IN), U2.3 (EN)

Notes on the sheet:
Analog Supply Filtering
SPI MODE 0
but RDYN and REQN
replace CS

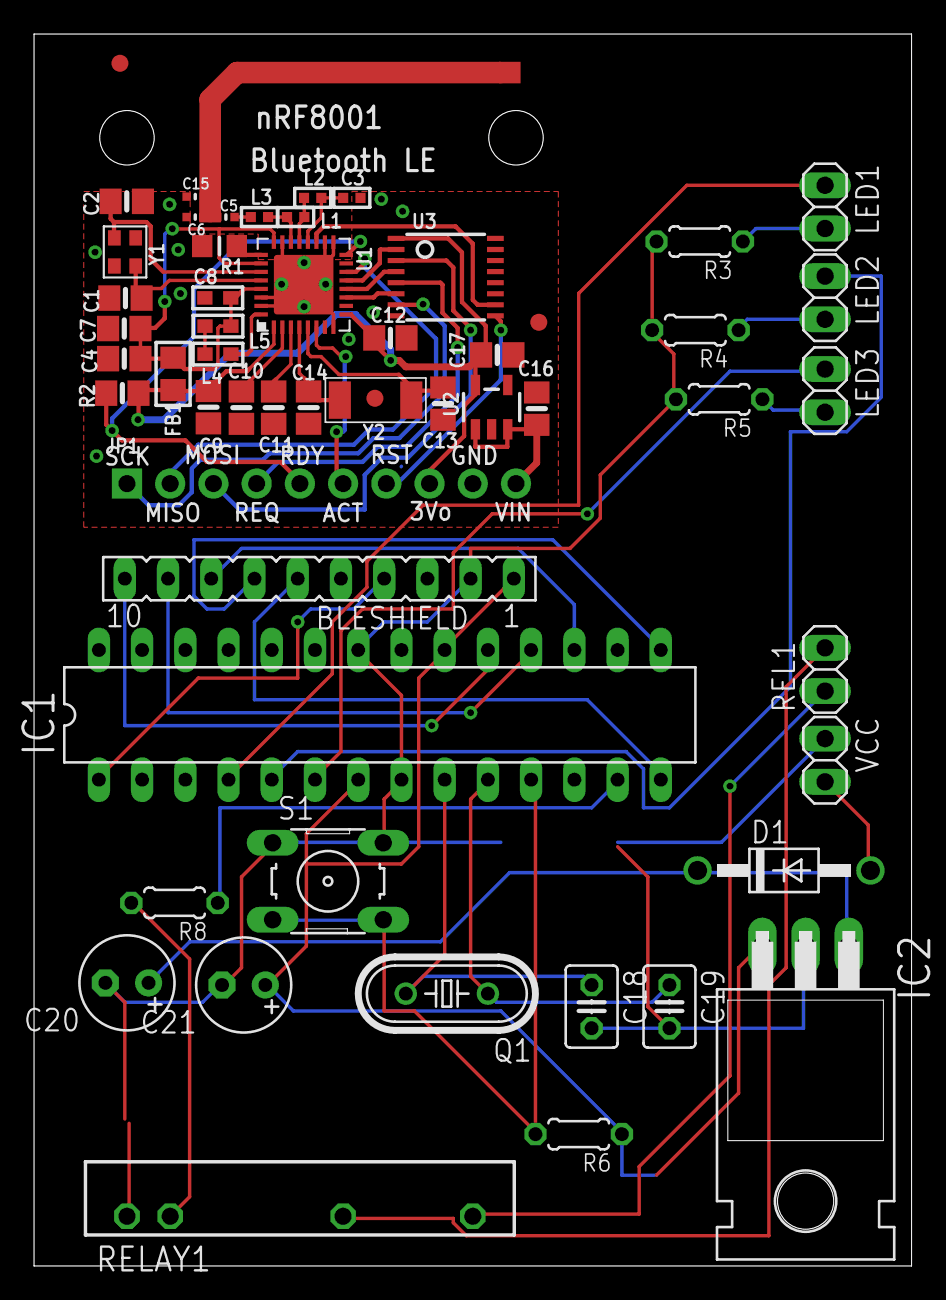
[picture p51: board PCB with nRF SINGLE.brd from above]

Board: 2 copper layers, 51.6 x 72.4 mm, 57 parts (1 on the bottom side), 52 nets.

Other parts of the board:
U$22: ADAFRUIT_TEXT_20MM

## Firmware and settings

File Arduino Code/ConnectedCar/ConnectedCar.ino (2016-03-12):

/* Copyright (c) 2014, Nordic Semiconductor ASA
 *
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
 * THE SOFTWARE IS PROVIDED "AS IS", WITHOUT WARRANTY OF ANY KIND, EXPRESS OR
 * IMPLIED, INCLUDING BUT NOT LIMITED TO THE WARRANTIES OF MERCHANTABILITY,
 * FITNESS FOR A PARTICULAR PURPOSE AND NONINFRINGEMENT. IN NO EVENT SHALL THE
 * AUTHORS OR COPYRIGHT HOLDERS BE LIABLE FOR ANY CLAIM, DAMAGES OR OTHER
 * LIABILITY, WHETHER IN AN ACTION OF CONTRACT, TORT OR OTHERWISE, ARISING FROM,
 * OUT OF OR IN CONNECTION WITH THE SOFTWARE OR THE USE OR OTHER DEALINGS IN THE
 * SOFTWARE.
 */


/*
IMPORTANT NOTE:

IN ORDER TO COMPILE THIS CODE, YOU WILL NEED THE LIBRARIES ALSO INCLUDED WITH THIS CODE.
THESE LIBRARIES ARE:

BLE
TIME

ALONG SIDE THESE, YOU WILL NEED THE ARDUINO IDE, SPECIFICALLY VERSION 1.0.6 . This version includes SPI and EEPROM
LIBRARIES WHICH ARE NEEDED TO COMPILE THIS CODE. THE IDE IS ALSO INCLUDED AS A ZIP FILE IN THIS DOCUMENTATION.

*/
 
 
/*
Import libraries
*/

#include <SPI.h>
#include <lib_aci.h>
#include <aci_setup.h>
#include "services.h"
#include <EEPROM.h>
#include <Time.h>


/* these variables are used to manage time after login into device*/
long t;
int second_now;
long int seconds_passed = 0;


/*three different leds used. Green for connection, red for Disconnected and yellow for Bluetooth locked out*/

int green_LED = A5;
int yellow_LED = 2;
int red_LED = 3;

/* Four relays manage this system. */
int relay_garage_stop = 7;
int relay_garage_open = 4;
int relay_garage_close = 5;
int relay_lights_switch = 10;

/*Push Buttons */

int pushbutton_garage_stop = A0;
int pushbutton_garage_open = A1;
int pushbutton_garage_close = A2;
int pushbutton_light_switch = A3;
int pushbutton_wireless_unlock = A4;

// char value eeprom_password[0] to store byte sized password value.
char eeprom_password[0];

//value to store result of login into the gatebox system. 0 is unsuccessful login and 1 is successful login.
uint8_t result = 0;

//value to store result of password change of the gatebox system. 
uint8_t change_result = 0;

//1: garage closed. 0: garage open.
uint8_t garage_state = 1;

//1: g
uint8_t light_state = 1;
uint8_t light_state_now = 1;
uint8_t garage_state_now = 1;

//pipe_num value determines which pipe number is being used to communicate with the gatebox. Different pipes are used to talk to different characteristics.
uint8_t pipe_num;

//new password to rewrite the old password.
uint8_t overwrite_password_value[16];


/* Data is transmitted over the pipe as two hexadecimal digits.
The four digit password can start with 0s. If that is the case, then these 0s will be ignored o
ver the transmission. If the transmission of a byte was less than 2 hexadicamal digits
we know that the password began from a zero. This 0 must be inserted at the front of the file. */
String pipe_data_part_1;
String pipe_data_part_2;

/*The two portions pipe_data_part_1 and pipe_data_part_2 are then concatenated to form the password */
String pipe_data_full_hex;

//the entered password must be changed into string so that its individual digits can be read in an order.
String pipe_data_full_dec;



//char incoming_data[34];

uint8_t data_size;

//incorrect_password_counter counts the number of times data has been entered incorrectly into the system.
uint8_t incorrect_password_counter = 0;

//test boolean for garage and light
boolean connection_light = false;
boolean wireless_locked = false;

/*
boolean light_push_button = false;
boolean garage_push_button = false;
*/

boolean password_check_state = false;
boolean password_change_state = false;
//boolean overwrite_check_password_now = false;
boolean overwrite_change_password_now = false;

boolean overwrite_password_now = false;

/*
boolean garage_open_state = false;
boolean garage_close_state = false;
boolean garage_stop_state = false;
boolean lights_change_state = false;
*/

boolean garage_state_send = false;
boolean light_state_send = false;

//these integers will be used to store the individual digits from the string in the for loop. The for loop with compare the two password strings at each position.
int eeprom_password_digit;
int entered_password_digit;

int address = 0;

//may have to delete this later.
//char entered_password_as_string[34];

//char entered_password_part_1[34];

//char entered_password_part_2[34];

//the password currently stored in eeprom will be copied into this variable.
char password_in_eeprom[0];


  

#ifdef SERVICES_PIPE_TYPE_MAPPING_CONTENT
  static services_pipe_type_mapping_t
      services_pipe_type_mapping[NUMBER_OF_PIPES] = SERVICES_PIPE_TYPE_MAPPING_CONTENT;
#else
  #define NUMBER_OF_PIPES 0
  static services_pipe_type_mapping_t * services_pipe_type_mapping = NULL;
#endif


/*
Store the nRF8001 setup information generated on the flash of the AVR.
This reduces the RAM requirements for the nRF8001.
*/
static hal_aci_data_t setup_msgs[NB_SETUP_MESSAGES] PROGMEM = SETUP_MESSAGES_CONTENT;
// an aci_struct that will contain
// total initial credits
// current credit
// current state of the aci (setup/standby/active/sleep)
// open remote pipe pending
// close remote pipe pending
// Current pipe available bitmap
// Current pipe closed bitmap
// Current connection interval, slave latency and link supervision timeout
// Current State of the the GATT client (Service Discovery)

static aci_state_t aci_state;

static hal_aci_evt_t aci_data;
static hal_aci_data_t aci_cmd;

/*
We will store the bonding info for the nRF8001 in the EEPROM/Flash of the MCU to recover from a power loss situation
*/
static bool bonded_first_time = true;

static bool radio_ack_pending  = false;
static bool timing_change_done = false;

/* Define how assert should function in the BLE library */
void __ble_assert(const char *file, uint16_t line)
{
  Serial.print("ERROR ");
  Serial.print(file);
  Serial.print(": ");
  Serial.print(line);
  Serial.print("\n");
  while(1);
}

/*************NOTE**********
Scroll to the end of the file and read the loop() and setup() functions.
The loop/setup functions is the equivalent of the main() function
*/

/*
Read the Dymamic data from the EEPROM and send then as ACI Write Dynamic Data to the nRF8001
This will restore the nRF8001 to the situation when the Dynamic Data was Read out
*/


aci_status_code_t bond_data_restore(aci_state_t *aci_stat, uint8_t eeprom_status, bool *bonded_first_time_state)
{
  aci_evt_t *aci_evt;
  uint8_t eeprom_offset_read = 1;
  uint8_t write_dyn_num_msgs = 0;
  uint8_t len = 0;
  

  // Get the number of messages to write for the eeprom_status
  write_dyn_num_msgs = eeprom_status & 0x7F;

  //Read from the EEPROM
  while(1)
  {
    len = EEPROM.read(eeprom_offset_read);
    eeprom_offset_read++;
    aci_cmd.buffer[0] = len;

    for (uint8_t i=1; i<=len; i++)
    {
        aci_cmd.buffer[i] = EEPROM.read(eeprom_offset_read);
        eeprom_offset_read++;
    }
    //Send the ACI Write Dynamic Data
    if (!hal_aci_tl_send(&aci_cmd))
    {
      Serial.println(F("bond_data_restore: Cmd Q Full"));
      return ACI_STATUS_ERROR_INTERNAL;
    }

    //Spin in the while loop waiting for an event
    while (1)
    {
      if (lib_aci_event_get(aci_stat, &aci_data))
      {
        aci_evt = &aci_data.evt;

        if (ACI_EVT_CMD_RSP != aci_evt->evt_opcode)
        {
          //Got something other than a command response evt -> Error
          Serial.print(F("bond_data_restore: Expected cmd rsp evt. Got: 0x"));
          Serial.println(aci_evt->evt_opcode, HEX);
          return ACI_STATUS_ERROR_INTERNAL;
        }
        else
        {
          write_dyn_num_msgs--;

          //ACI Evt Command Response
          if (ACI_STATUS_TRANSACTION_COMPLETE == aci_evt->params.cmd_rsp.cmd_status)
          {
            //Set the state variables correctly
            *bonded_first_time_state = false;
            aci_stat->bonded = ACI_BOND_STATUS_SUCCESS;

            delay(10);

            return ACI_STATUS_TRANSACTION_COMPLETE;
          }
          if (0 >= write_dyn_num_msgs)
          {
            //should have returned earlier
            return ACI_STATUS_ERROR_INTERNAL;
          }
          if (ACI_STATUS_TRANSACTION_CONTINUE == aci_evt->params.cmd_rsp.cmd_status)
          {
            //break and write the next ACI Write Dynamic Data
            break;
          }
        }
      }
    }
  }
}



/*
This function is specific to the atmega328
@params ACI Command Response Evt received from the Read Dynmaic Data
*/


void bond_data_store(aci_evt_t *evt)
{
  static int eeprom_write_offset = 1;

  //Write it to non-volatile storage
  EEPROM.write( eeprom_write_offset, evt->len -2 );
  eeprom_write_offset++;

  EEPROM.write( eeprom_write_offset, ACI_CMD_WRITE_DYNAMIC_DATA);
  eeprom_write_offset++;

  for (uint8_t i=0; i< (evt->len-3); i++)
  {
    EEPROM.write( eeprom_write_offset, evt->params.cmd_rsp.params.padding[i]);
    eeprom_write_offset++;
  }
}



bool bond_data_read_store(aci_state_t *aci_stat)
{
  /*
  The size of the dynamic data for a specific Bluetooth Low Energy configuration
  is present in the ublue_setup.gen.out.txt generated by the nRFgo studio as "dynamic data size".
  */
  
  bool status = false;
  aci_evt_t * aci_evt = NULL;
  uint8_t read_dyn_num_msgs = 0;

  //Start reading the dynamic data
  lib_aci_read_dynamic_data();
  read_dyn_num_msgs++;

  while (1)
  {
    if (true == lib_aci_event_get(aci_stat, &aci_data))
    {
      aci_evt = &aci_data.evt;

      if (ACI_EVT_CMD_RSP != aci_evt->evt_opcode)
      {
        //Got something other than a command response evt -> Error
        status = false;
        break;
      }

      if (ACI_STATUS_TRANSACTION_COMPLETE == aci_evt->params.cmd_rsp.cmd_status)
      {
        //Store the contents of the command response event in the EEPROM
        //(len, cmd, seq-no, data) : cmd ->Write Dynamic Data so it can be used directly
        bond_data_store(aci_evt);

        //Set the flag in the EEPROM that the contents of the EEPROM is valid
        EEPROM.write(0, 0x80|read_dyn_num_msgs );
        //Finished with reading the dynamic data
        status = true;

        break;
      }

      if (!(ACI_STATUS_TRANSACTION_CONTINUE == aci_evt->params.cmd_rsp.cmd_status))
      {
        //We failed the read dymanic data
        //Set the flag in the EEPROM that the contents of the EEPROM is invalid
        EEPROM.write(0, 0xFF);

        status = false;
        break;
      }
      else
      {
        //Store the contents of the command response event in the EEPROM
        // (len, cmd, seq-no, data) : cmd ->Write Dynamic Data so it can be used directly when re-storing the dynamic data
        bond_data_store(aci_evt);

        //Read the next dynamic data message
        lib_aci_read_dynamic_data();
        read_dyn_num_msgs++;
      }
    }
  }
  return status;
}
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
void loop()
{
  //static uint8_t value = 2;

  aci_loop();
  
/*
Before sending data, the following if statement carries out a check to confirm that the pipe
it is sending data on is infact available.
*/

  //if connection_light is true
  if (connection_light == true) {
    
    //turn the green LED on and the red LED off.
    digitalWrite(green_LED, HIGH);
    digitalWrite(red_LED, LOW);
    
  } else {
    
    //if connection_light is not true, turn the green LED off and the red LED on.
    digitalWrite(green_LED, LOW);
    digitalWrite(red_LED, HIGH);    
    
  }
    
//the timer increments by 1 every second.
  t = now();
  
  //if 65 seconds or greater have passed
  if (seconds_passed >= 65) {
    
    //disconnect the device
    lib_aci_disconnect(&aci_state, ACI_REASON_TERMINATE);
    
    //reset the timer.
    seconds_passed = 0;
    
    //reset result and change_result to 0.
    result = 0;
    change_result = 0;
    
    //set connection light to false. This will turn off the green LED and turn on the red LED.
    connection_light = false;

  }
  
  // while logged into the device and a second has passed
  if ((result == 1) && (second_now != second(t))) {
    
    //update the value of second
    second_now = second(t);
    
    //increment seconds_passed by 1
    seconds_passed++;
    Serial.println(seconds_passed);
    
    //set connection light to true.
    connection_light = true;
    
  }
  

  //if password was entered incorrectly 3 times, put the device under wireless lock.
  if (incorrect_password_counter >= 3) {
    
    wireless_locked = true;
    
  }
  
  //if the device is under wireless lock, disconnect the device immediately.
  if (wireless_locked == true) {
    
    //if authentication failed after connection, disconnect.
    lib_aci_disconnect(&aci_state, ACI_REASON_TERMINATE);
    result = 0;
    change_result = 0;
    
    //turn the yellow light ON indicating the device is locked.
    digitalWrite(yellow_LED, HIGH);
    
    
  }
  
  //if data is to be sent over the garagedoor characteristic's pipe
  if (garage_state_send == true) 
  
  {
    
    //if send_byte was successful
    if (send_byte(PIPE_CONNECTEDCAR_GARAGEDOOR_TX, garage_state)) {
      
      //set garage_state_send to false
      garage_state_send = false;
      Serial.println("garage state sent");
    }
    
  }
  
  //if data is to be sent over the lightson characteristic's pipe
  if (light_state_send == true) 
  
  {
    
    //if send_byte was successful
    if (send_byte(PIPE_CONNECTEDCAR_LIGHTSON_TX, light_state)) {
      
      //set light_state_send to false
      light_state_send = false;
      Serial.println("light state sent");
    }
    
  }
  
  //if data is to be sent over the results characteristic's pipe
  if (password_check_state == true) {
   
   //if send_byte was successful
   if (send_byte(PIPE_CONNECTEDCAR_RESULTS_TX, result)) 
   
   {
     //set password_check_to false
     password_check_state = false;
     Serial.println("password checked");
     
     //set overwrite_password_now to true.
     overwrite_password_now = true;
     
   }
   
  }
    
  //overwrite_password_now is used because once password is written by the smartphone, it is still present on the pipe. In order to erase this data,
  //the password characteristic's pipe sends a notification (which the smartphone app is programmed to recieve) once it has sent a password. The notification
  //consists of 0000. This overwrites the previous value on the characteristic.
  
  //set overwrite_password_now to true.
  if (overwrite_password_now == true) {
    
    //transmit 0000 over the pipe.
    if (overwrite_password(PIPE_CONNECTEDCAR_PASSWORD_TX, 0)) 
    
    {
      //set overwrite_password_now to false.
      overwrite_password_now = false;
      Serial.println("check password overwritten");

    } 
  }
 
  //if password_change_state is true
  if (password_change_state == true) {
   
   //if send_byte was successful
   if (send_byte(PIPE_CONNECTEDCAR_CHANGERESULTS_TX, change_result)) 
     {
       
       //set password_change_state to false.
       password_change_state = false;
       Serial.println("password changed");
       
       //set overwrite_change_password_now to true
       overwrite_change_password_now = true;
       
     }
  }
  
  //overwrite_change_password_now is used because once password is written by the smartphone, it is still present on the pipe. In order to erase this data,
  //the passwordchange characteristic's pipe sends a notification (which the smartphone app is programmed to recieve) once it has sent a password. The notification
  //consists of 0000. This overwrites the previous value on the characteristic.
  
  //if overwrite_change_password_now is set to true.
  if (overwrite_change_password_now == true) {
    
    //transmit 0000 over the pipe.
    if (overwrite_password(PIPE_CONNECTEDCAR_PASSWORDCHANGE_TX,0))
    
    {
      //overwrite_change_password_now
      overwrite_change_password_now = false;
      Serial.println("check password overwritten");

    }
    
  }

  //this is to manually release the wireless lock on the device by pressing the bluetooth unlock command.
  if (digitalRead(pushbutton_wireless_unlock) == LOW) {
    
    //debounce
    delay(50);
    
    //reset the incorrect_password_counter to 0
    incorrect_password_counter = 0;
    
    //wireless_locked is set to false.
    wireless_locked = false;
    
    //turn OFF the yellow LED
    digitalWrite(yellow_LED, LOW);

  }
  
  //if the garage stop pushbutton is pressed
  if (digitalRead(pushbutton_garage_stop) == LOW) {
    
    //debounce
    delay(50);
    
    //set the garage_state_now to 1
    garage_state_now = 1;
    Serial.println("garage_state_stop");
  }
  
  //if the garage open pushbutton is pressed
  if (digitalRead(pushbutton_garage_open) == LOW) {
    
    //debounce
    delay(50);
    
    //set the garage_state_now to 2
    garage_state_now = 2;
    Serial.println("garage_state_open");
  }
  
  //if the garage close pushbutton is pressed  
  if (digitalRead(pushbutton_garage_close) == LOW) {
    
    //debounce
    delay(50);
    
    //set the garage_state_now to 3
    garage_state_now = 3;
    Serial.println("garage_state_close");
  }
  
  //if the light switch pushbutton is pressed    
  if (digitalRead(pushbutton_light_switch) == LOW) {
        
    //debounce
    delay(50);
    
    //if the light was ON, turn it OFF. If the light was OFF turn it ON.
    if (light_state_now == 1) {
      
      light_state_now = 2;
      Serial.println("light_state_on");
      
    } else {
      
      light_state_now = 1;
      Serial.println("light_state_off");
      
    }

  }
  
  //if the garage state has been changed on the smartphone.
  if (garage_state_now != garage_state) {
    
    garage();
    
  }
  
  // if light_state has been changed on the smartphone.
  if (light_state_now != light_state) {  

    lights();
    
    delay(1000);
    
  }
  
}

/*
Further work needed on this code:

1. Testing

2. Tidy up code 
 - remove unncessary ACI commands.
 - uniform syntax
 - well commented and checked for grammar
 
*/

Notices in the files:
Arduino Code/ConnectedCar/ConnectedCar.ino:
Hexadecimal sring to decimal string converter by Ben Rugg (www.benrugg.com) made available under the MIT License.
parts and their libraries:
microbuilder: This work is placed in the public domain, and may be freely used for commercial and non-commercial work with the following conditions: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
